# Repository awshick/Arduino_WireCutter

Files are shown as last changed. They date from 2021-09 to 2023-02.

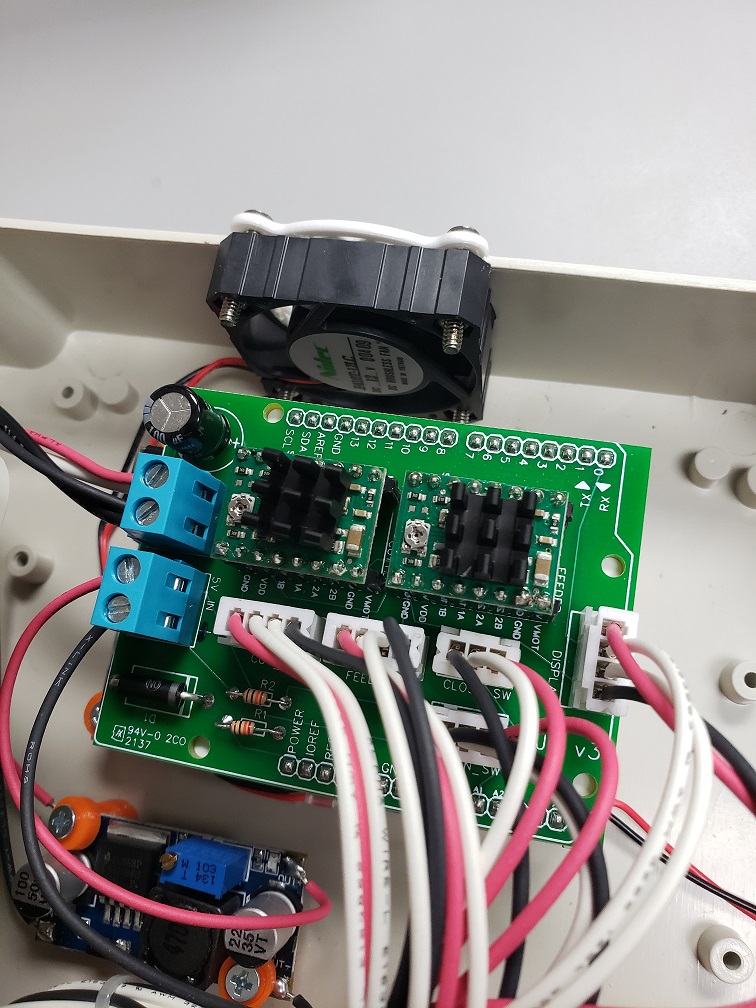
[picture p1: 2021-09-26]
pics/board_view.jpg

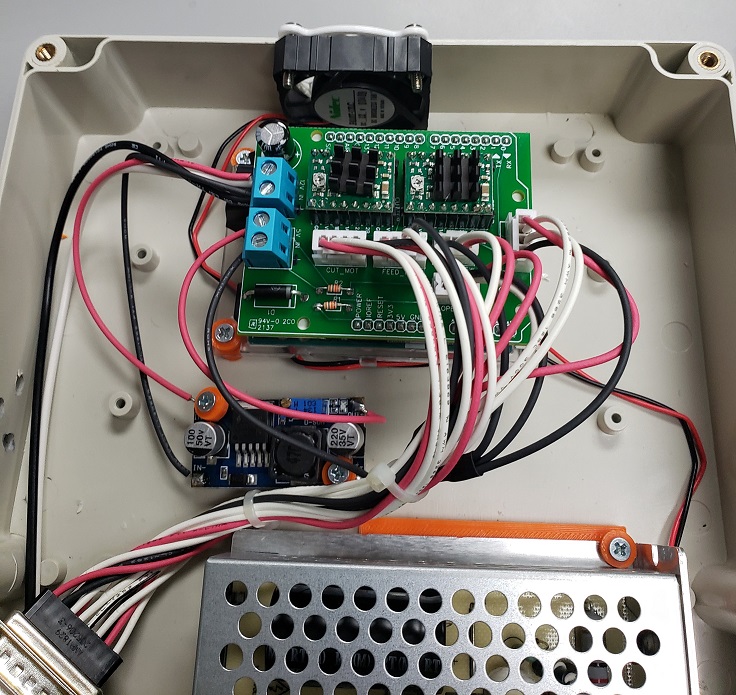
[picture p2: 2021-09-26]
pics/box_view1.jpg

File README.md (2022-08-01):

# Arduino_WireCutter
Arduino wire cutter stripper with nextion display

I'm not a professional. I've worked on my own personal 3d printers for awhile so I'm familiar with arduino and steppers. Never have I done a project like this so its my first from start to finish. I basically saw Mr Innovatives video and wanted a machine similar, but no code or layout was provided. I've made some very simple 3d drawings for the supports and during my trial and error build I decided limit switches where the way I wanted to go. This way I dont care about steps when it comes to cutting the wire (other than feeding wire).
My first nextion HMI - lots of hardships getting through it and the arduino code, again I'm no pro by far. I'm sure there are alot of things that are questionable and/or not correctly done, but I went with what I could figure out.
Please feel free to contribute to the code, if you want to collabrate on this let me know and I'll open the door.
I can be contacted through garzajd3@gmail.com or message on github.

In the pics below is my version of this tool. I went with adding limit switches on the "cutter" stepper so that I do not need to actually know the # of steps for a close/open.
There are a total of 5 3d printed parts: 1 for the feed stepper mount, 1 for the wire tube holder (adjustable to align with cutter), 1 cutter holder, 1 piece the holds both limits switches (mounted to the cutter stepper). 
I've also opted to use a 5:1 stepper for the cutting unit. I was finding that with a standard 1:1 nema 17 sometimes steps would be skipped when trying to cut wire. I'm sure this can be worked out by adjusting linkage, position, etc but I wanted something that would work consistently with alittle more power. 



Sorry this pic is blurry, but it was the only one I took. This is the simple PCB I laid out as a UNO plug-in (shield) for the stepper drivers and connectors. I probably went overkill on the components, but oh well.


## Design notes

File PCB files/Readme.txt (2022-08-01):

Gerber File_BOM:

This is a custom layout I did for this setup.
Nothing special, and can be done on breadboard or with just wire(s).
I also added a 5vdc input, as in my testing the LM7805's looked to power everything
without issue, but nothing actually worked unless arduino was plugged in. I suspect
low current, even with 2 in parallel, but may be a ground/pwr issue on my layout.

Folders:
Mr Innovative Board:
PCB from Mr Innovatives link on youtube. I believe this is the smb version, and not all components
are required for this wire cutter project. However I have not tested this board.

Gerber_Ext_5v:  <-- This is what I will use, as a shield for UNO board.
For use with external 5v (input) to power Arduino board & Display.

old:
Original board I made, included limit switch(s) plug (A1SW, A0SW).
I've found the LM7805's (U2, U3) work, but not impressed with stability, low voltage. Plan to run a buck converter
to drop 12v from main supply down to 5v for display/Uno - 5VIN plug (input voltage, not output).

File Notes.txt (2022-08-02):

8/1/2022:
Modified arduino code(s) for wire length loops. Previously if entering non whole number it would ignore the decimal point on the final length value.
I have it now including the decimal value in the calculation, but still uses a whole number for the step loops - so accuraccy is not 100% but tolerance is alot better now. 
Example - previously was using a calculation of 6.23 stepper motor steps to equal 1mm of wire. If input was for a 100.5mm length it would be should be converted to 
626.115 (100.5 * 6.23). However as it was an integer you would actually get 626 steps. Error would drift more or less depending upon wire length desired. 

10/24/2021:
I've made a few modifications, mostly cosmetic. I've mounted everything on a plastic box, and housed the electronics within it.
I've recieve no contact, so not sure anyone is even following this. If you are reading this and want to make one - reach out to 
me and I'll give you all the help I can.
If you've emailed me and no response, may have gone to spam. Try me at garzajd3@gmail.com (I check this frequently).

This is for 2 stepper setup only. No servo used, as wire is feed into strip point of strippers, and if to be cut stripper is simply fully closed.
Input voltage is 12vDC, not sure of max current draw but I have an 8.5A power supply (way overkill just using what I had on hand).
I did alot of my inital testing with a 12vdc 2amp power brick and it seemed to work just fine.

I used servos in 1/2 step mode, so MS1,MS2,MS3 are needed.
If you want to use in full step, then MS1-MS3 are not required and arduino code will need to be modified
to remove mode selection.

Videos I used to help me with this:
Nextion Display (Huge thanks to Cheap Controls channel. Tons of Nextion stuff here!!!):
https://www.youtube.com/watch?v=VovDHGs1zDk&t=458s

Stepper wiring / usage (Thanks to Gadget Reboot channel):
https://www.youtube.com/watch?v=V7amtlMKsXU

Where this version of the ideal came of,atleast for me (Mr Innovative channel):
https://www.youtube.com/watch?v=Jl6ZATZypAQ&t=1s

Dumb things that took me way to long to figure out:

Using Nextion Editor for HMI programming/layout (https://nextion.tech/nextion-editor/)
I made my own keyboard input, because I could not figure out how to use the built-in one until I was already done.
By then I was not going to go back and update everything.

If using a different Nextion display change this by opening the WireCutter_v5.HMI file in nextion editor
On the top ICON line (after Redo) select the 'Deivce' button to change model/orientation.
Original was built using 5" nextion model NX8048T050. If using a smaller screen (2.4") you will likely need to 
scale images down on the screens (using nextion editor).

The Arduino code may not be as efficient or clean as it should, but I'm not a professional so it just needs to work
reliably. Feel free to improve on.

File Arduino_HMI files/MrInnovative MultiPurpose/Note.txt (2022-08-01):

This setup is based on using the 
Multipurpose v2.0 pcb used in Mr Innovative design.
https://oshwlab.com/sharmaz747/multipurpose-pcb

The Nextion (HMI) is setup for a 2.4" display.

The arduino code does not implement limit switch(s) and nothing
added for servo motor use (if you choose to include in your build).

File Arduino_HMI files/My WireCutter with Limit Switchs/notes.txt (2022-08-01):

8/1/22:
Modified arduino code to adjust length value. Was set to an integer, so if you entered 10.5 it was taking the whole number only (10).
Changed all associated values to float. As the entry is broken into steps (not distance) it will still be a whole number (rounded) for
the loop portion. This should be a closer match to the input length, but still will not be exact.

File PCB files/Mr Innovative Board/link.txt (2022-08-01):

https://oshwlab.com/sharmaz747/multipurpose-pcb_copy_copy_copy

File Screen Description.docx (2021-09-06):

Start Screen:

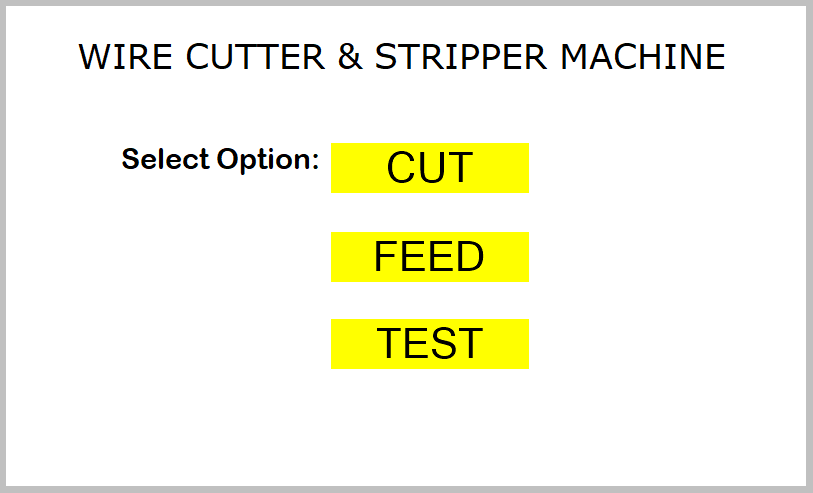
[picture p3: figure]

Select sub screen.

CUT = go directly to cutting wire

FEED = feed wire in/out

TEST = test stepper(s) , check steps and modes.

CUT | Screen 1:

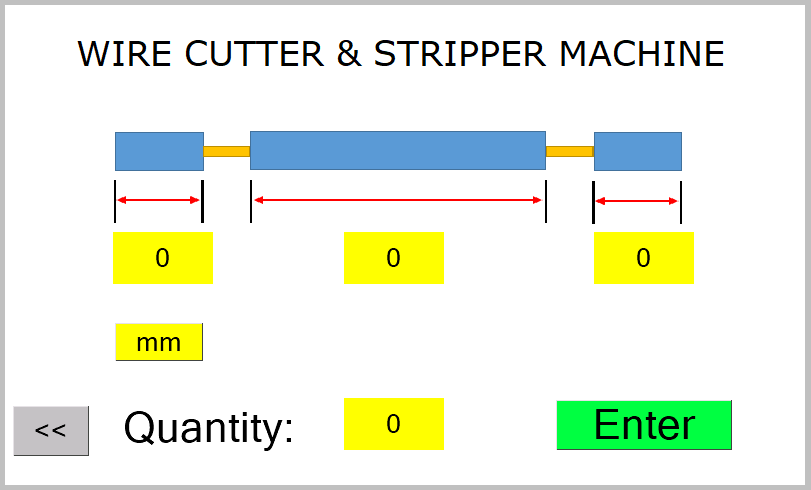
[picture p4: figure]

Enter details here. Can change from mm to inch. Looks like this is +/- .2inch or +/- 2mm

CUT | Screen 2:

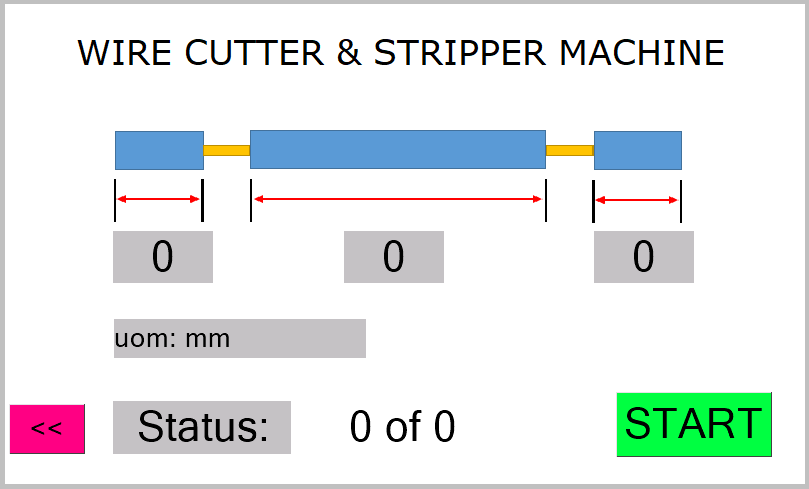
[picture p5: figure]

This is the details that are entered, non-editable on this screen. START begins the process.

Once started a STOP button will be shown, if pressed cycle will stop after current cut.

FEED | Screen 1:

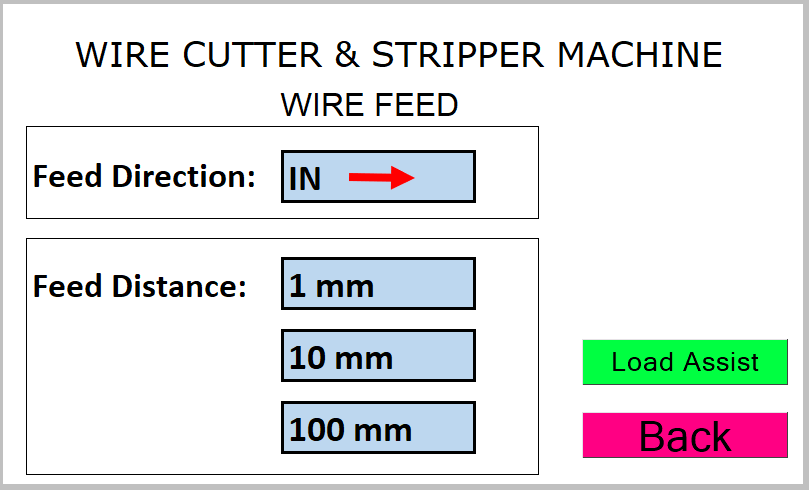
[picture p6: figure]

Select direction to feed wire IN/OUT. Distance button executes action on press. So if you press 10mm it will cycle direction for 10mm. Load Assist button takes to Screen 2.

FEED | Screen 2:

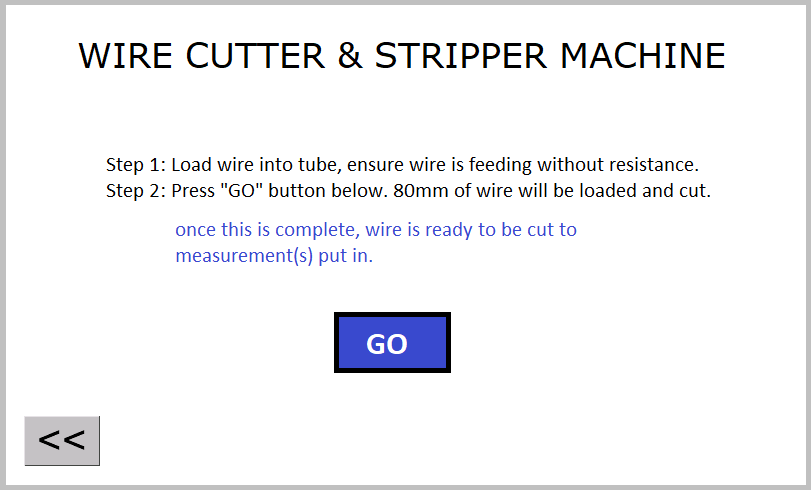
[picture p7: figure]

This is my simple version of loading. Once wire is loaded into tube, this will feed in 80mm and cut. This gives a 0 point to start cutting operation.

TEST | Screen 1:

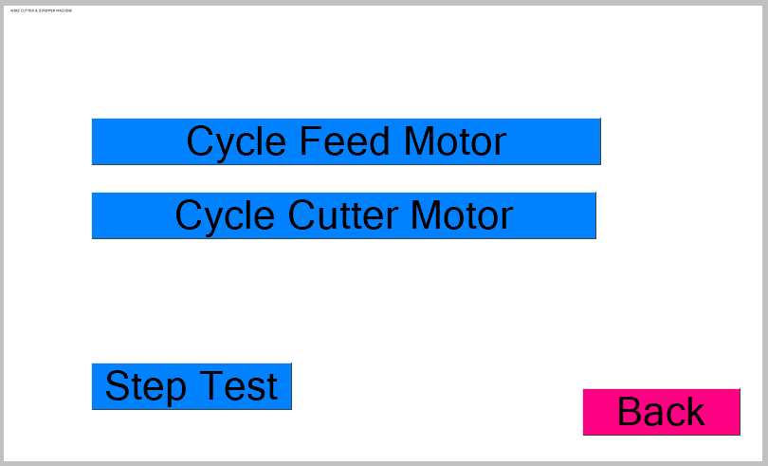
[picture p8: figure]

Simple test will cycle motor chosen.

Step Test leads to Screen 2

TEST | Screen 2:

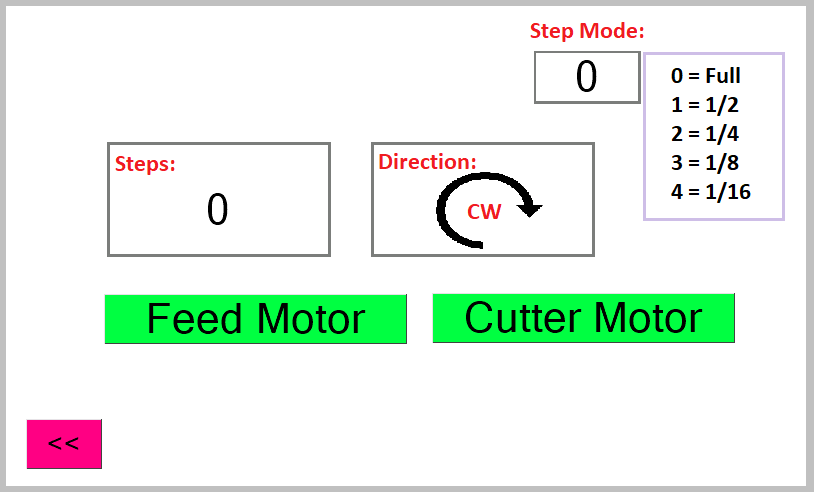
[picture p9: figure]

Not useful for operation, but I added this so I could enter the steps to travel and spin. Helped me determine what mode motor(s) worked best in, as well as how many steps are needed to reach a certain point (stripping, feeding x mm = x steps , etc).

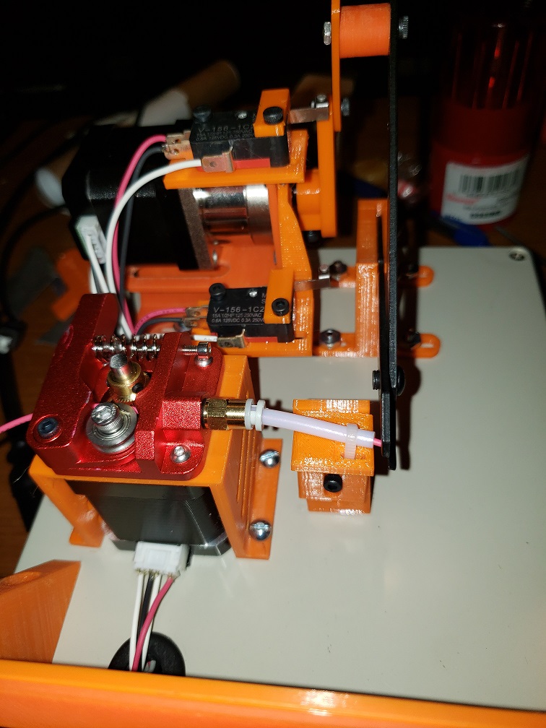
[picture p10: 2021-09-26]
pics/front_view.jpg

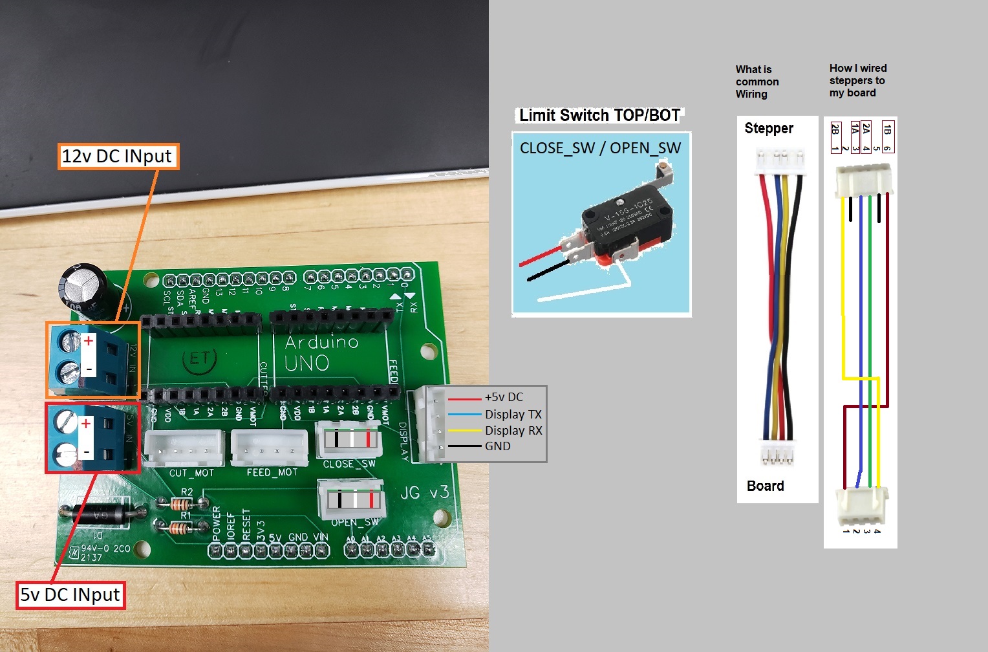
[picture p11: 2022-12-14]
pics/board_wire.jpg

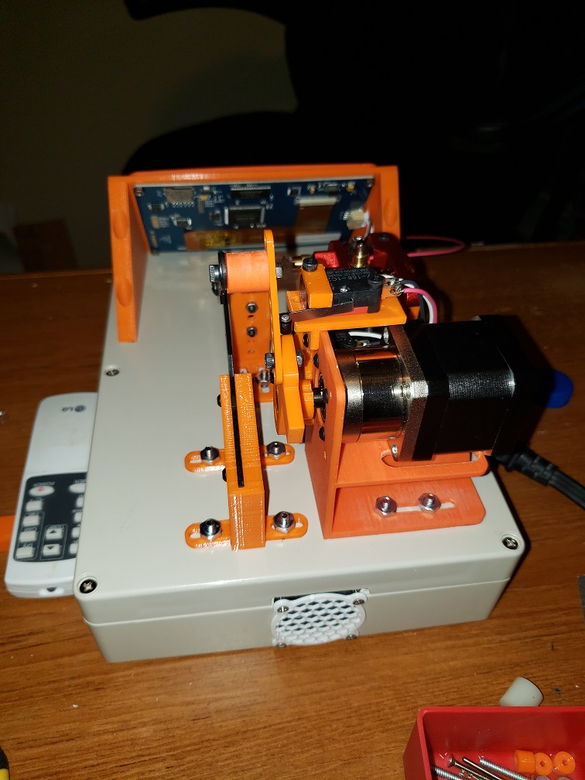
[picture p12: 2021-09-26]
pics/back_view.jpg

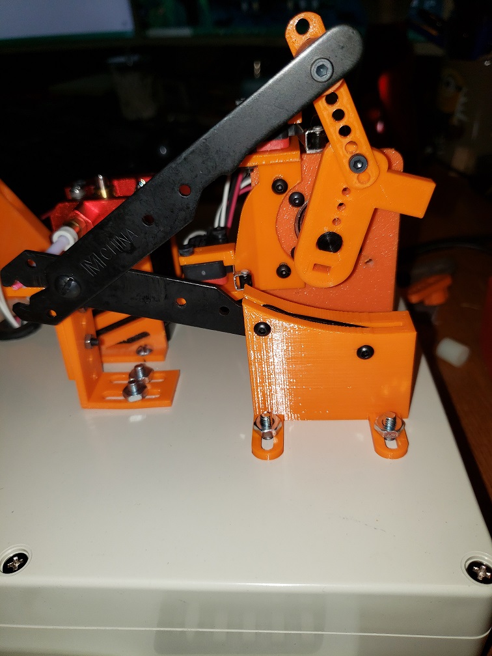
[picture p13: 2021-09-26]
pics/right_view.jpg

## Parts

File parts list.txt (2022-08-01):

These are the parts I used. Many options and models/mfg that do the same thing(s) and may be found cheaper.

Power Supply:	Source=Digikey	Price=$15.09
Description: LM100-23B12	12vdc 100W
https://www.digikey.com/en/products/detail/mornsun-america-llc/LM100-23B12/13168168

Nema 17 5.18:1 Gearbox:	Source=Amazon	Price=$28.59
Description: Usongshine Nema 17 Geared Stepper Motor Gear Ratio 5.18:1 Planetary Gearbox for 3 D Printer DIY CNC Robotics
https://www.amazon.com/gp/product/B07V359RFB/ref=ppx_yo_dt_b_asin_title_o03_s00?ie=UTF8&psc=1

Nema 17:	Source=Amazon	Price$9.99
Description: Twotrees Nema17 Stepper Motor, 4 Lead Stepper Motor Nema 17 Motor with 1m Cable 42BYGH 38MM 1.5A (17HS4401S) for CNC XYZ 3D Printer
https://www.amazon.com/Twotrees-Nema17-Stepper-17HS4401S-Printer/dp/B07Y2SVNGP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

Wire Feed Extruder:	Source=Amazon	Price=$6.99
Description: Gwisdom ENDER3 Extruder Upgraded Replacement, Aluminum MK8 Drive Feed
https://www.amazon.com/gp/product/B07FKD4FZD/ref=ppx_yo_dt_b_asin_title_o03_s00?ie=UTF8&psc=1

Limit Switch:	Source=Amazon	Price=$6.69 (10 pack)
Description: HiLetgo 10pcs V-156-1C25 Lead Limit Switch SPDT Switch Silver Base Contact Roller Swing
https://www.amazon.com/dp/B01MQPQGFQ?psc=1&ref=ppx_yo2_dt_b_product_details

Power Plug/Switch:	Source=Amazon	Price=$8.99
Description: 3Dman 15A 250V Rocker Switch Power Socket Inlet Module Plug 5A Fuse Switch with 18 AWG Wiring 3 Pin IEC320 C14
https://www.amazon.com/gp/product/B07RRY5MYZ/ref=ppx_yo_dt_b_asin_title_o03_s01?ie=UTF8&th=1

Buck Converter:	Source=Amazon	Price=$15.99 (10 pack)
Description: Zixtec 10 Pack LM2596 DC-DC Buck Converter Step Down Module Power Supply DIP Output 1.25V-30V 3A (ZT001)
https://www.amazon.com/gp/product/B07VVXF7YX/ref=ppx_yo_dt_b_asin_title_o04_s02?ie=UTF8&psc=1

Stepper Driver A4988:	Source=Amazon	Price=$9.28 (5 pack)
Description: HiLetgo 5pcs A4988 Stepstick Stepper Motor Driver Module with Heat Sink for 3D Printer Reprap Suitable for Mendel Huxley Arduino
https://www.amazon.com/gp/product/B07BND65C8/ref=ppx_yo_dt_b_asin_title_o04_s03?ie=UTF8&psc=1

Screen (Nextion):	Source=Amazon	Price=$81.97
Description: Nextion Display 5 inch NX8048T050 Resistive Touch Screen HMI TFT LCD Module 800x480 for Arduino Raspberry Pi
https://www.amazon.com/gp/product/B07B4DV86Z/ref=ppx_yo_dt_b_asin_title_o06_s00?ie=UTF8&psc=1

**Optional 2.4" instead:	Source=Amazon	Price=$30.98
Description: NEXTION 2.4 inch Display NX3224T024 Resistive Touch Screen UART HMI LCD Module 320x240 for Arduino Raspberry Pi ESP8266
https://www.amazon.com/WIshioT-Nextion-Display-NX3224T024-Raspberry/dp/B079172C9G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

Wire Cutter: Source=Mcmaster-carr	Price$8.26
Description: 26-12AWG Wire stripper , 5" Steel
https://www.mcmaster.com/wire-strippers/compact-electrical-wire-strippers/

Various M3 screws & nuts. 

ENCLOSURE / BOX PARTS:
Enclosure:	Source=Amazon	Price=$17.98
Description: LeMotech Waterproof Dustproof IP65 ABS Plastic Junction Box Universal Electric Project Enclosure Pale Gray 10.4 x 7.2 x 2.4 inch (263 x 182 x 60 mm)
https://www.amazon.com/gp/product/B0781D5YJH/ref=ppx_yo_dt_b_asin_title_o03_s01?ie=UTF8&th=1

Fan:	Source=Digikey	Price=$4.80
Description: HA40201V4-1000U-A99	40x40x20 12vdc fan
https://www.digikey.com/en/products/detail/sunon-fans/HA40201V4-1000U-A99/6198729

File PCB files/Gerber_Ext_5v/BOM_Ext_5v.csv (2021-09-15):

ID | Name | Designator | Footprint | Quantity | Manufacturer Part | Manufacturer | Supplier | Supplier Part | Price | Pins
1 | TB004-508-02BE | 5V_IN,12V_IN | CUI_TB004-508-02BE | 2 |  |  |  |  |  | 2
2 | 1000uF | C1 | CAP-TH_BD10.0-P5.00-D1.0-FD | 1 | 01EC4294SHC1000UF25V | KNSCHA | LCSC | C503217 | 0.06 | 2
3 | B3B-XH-A(LF)(SN) | CLOSE_SW,OPEN_SW | CONN-TH_3P-P2.50_B3B-XH-A-LF-SN | 2 | B3B-XH-A(LF)(SN) | JST Sales America | LCSC | C144394 | 0.041 | 3
4 | A4988 | CUTTER,FEEDER | A4988 STEPPER MOTOR DRIVER | 2 |  |  |  |  |  | 16
5 | B4B-XH-A-G | CUT_MOT,DISPLAY,FEED_MOT | CONN-TH_B4B-XH-A-G | 3 | B4B-XH-A-G | JST | LCSC | C594232 | 0.196 | 4
6 | 1N5349BG | D1 | DO-201_BD5.3-L9.5-P13.50-D1.4-RD | 1 | 1N5349BG | ON Semicon | LCSC | C232446 | 0.199 | 2
7 | UNO_R3 | P1 | UNO_R3 | 1 |  |  |  |  |  | 32
8 | 10K | R1,R2 | RES-TH_BD1.7-L3.5-P7.50-D0.5 | 2 | RN 1/8W 10K F T/B A1 | TyoHM | LCSC | C433502 | 0.008 | 2

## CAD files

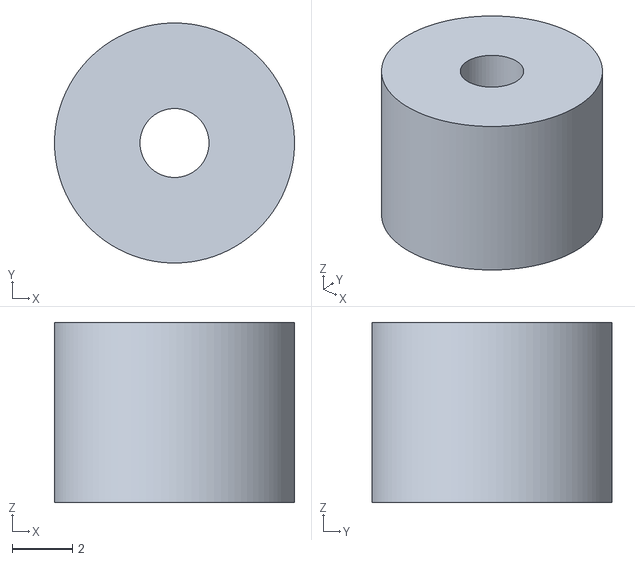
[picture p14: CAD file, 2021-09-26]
3d_printer_files/misc_plasticbox/full_shaft v1.stl
8.00 x 8.00 x 6.00

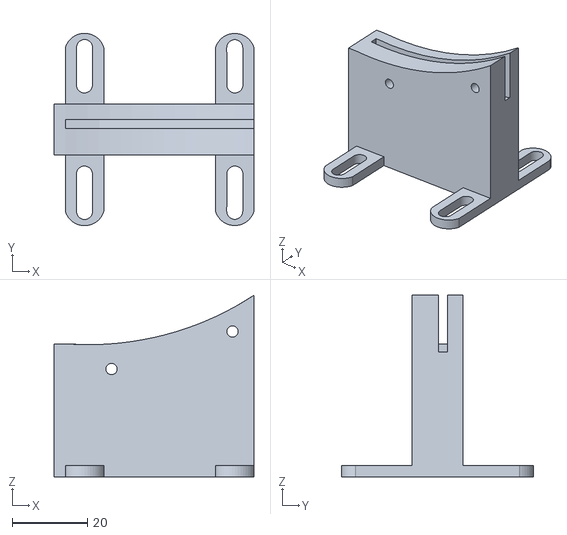
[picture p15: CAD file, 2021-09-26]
3d_printer_files/cutter_holder_adj.stl
53.0 x 51.0 x 48.1

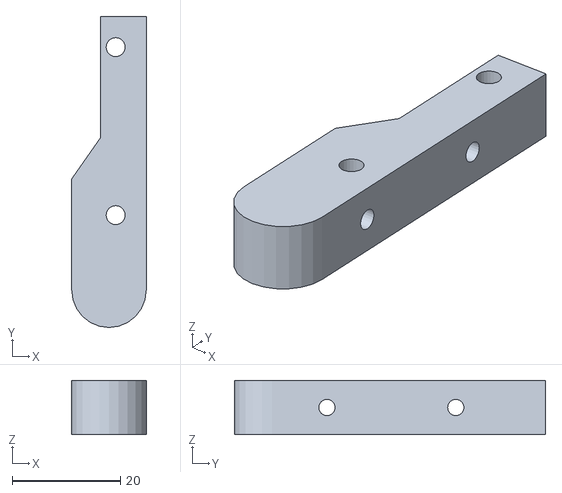
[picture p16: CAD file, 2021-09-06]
3d_printer_files/extruder/fixed_guide.stl
13.8 x 57.4 x 10.00

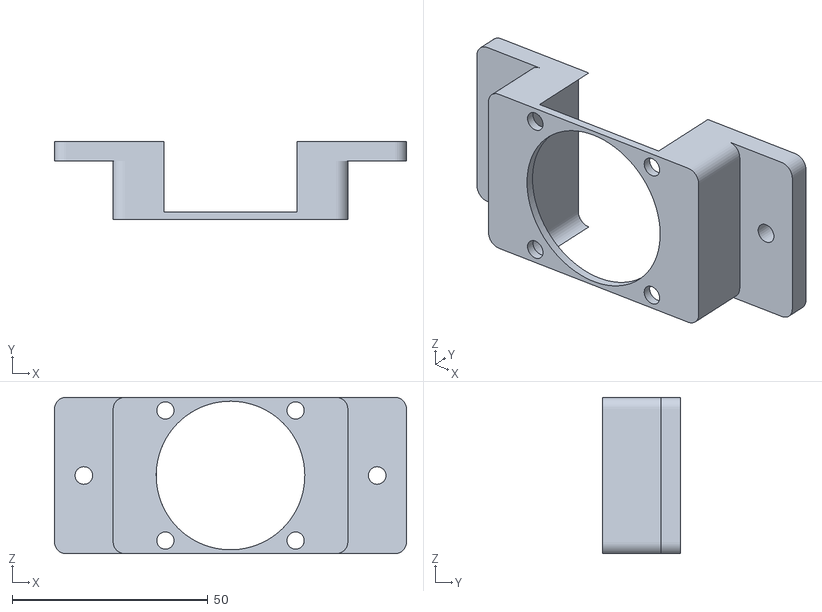
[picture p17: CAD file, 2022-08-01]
3d_printer_files/misc_plasticbox/fan_mount_acutal v2.stl
90.0 x 20.0 x 40.0

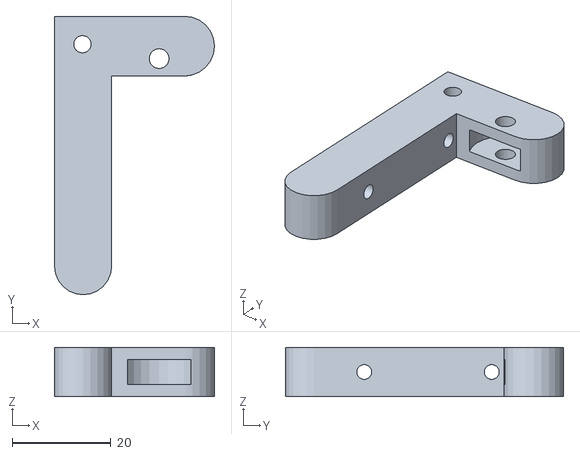
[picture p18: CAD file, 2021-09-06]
3d_printer_files/extruder/swing_handle.stl
32.3 x 56.3 x 10.0

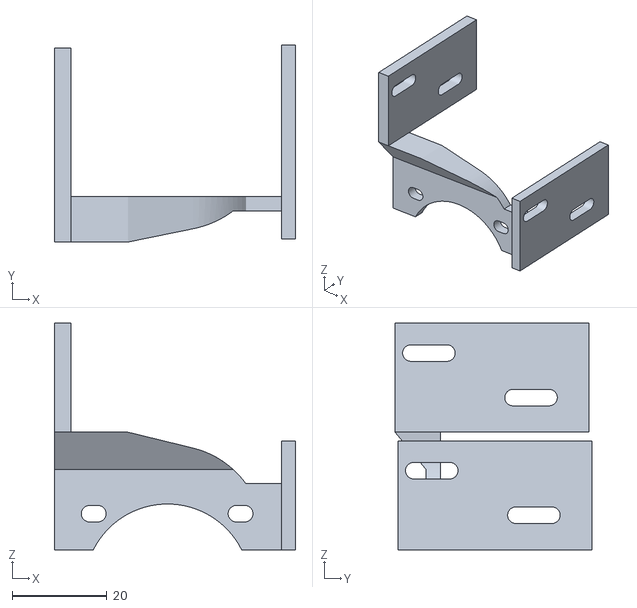
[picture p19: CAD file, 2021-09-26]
3d_printer_files/StopSwitchDual.stl
50.9 x 41.6 x 47.8

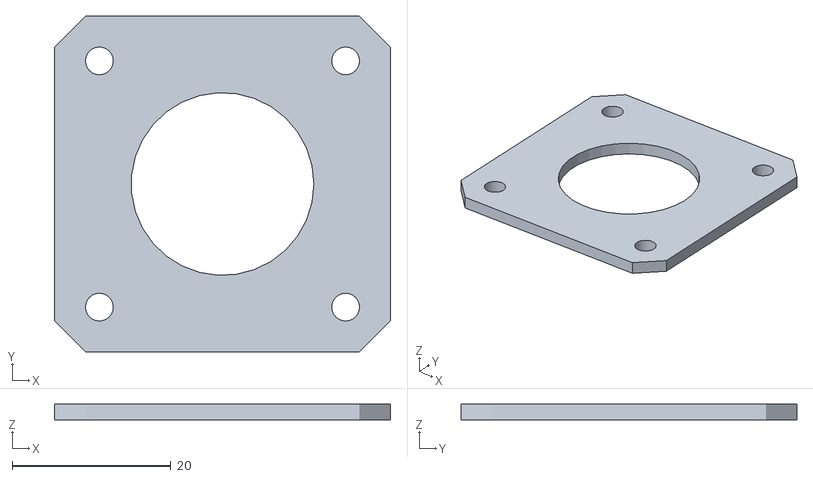
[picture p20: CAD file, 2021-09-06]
3d_printer_files/extruder/spacer.stl
42.3 x 42.3 x 2.00

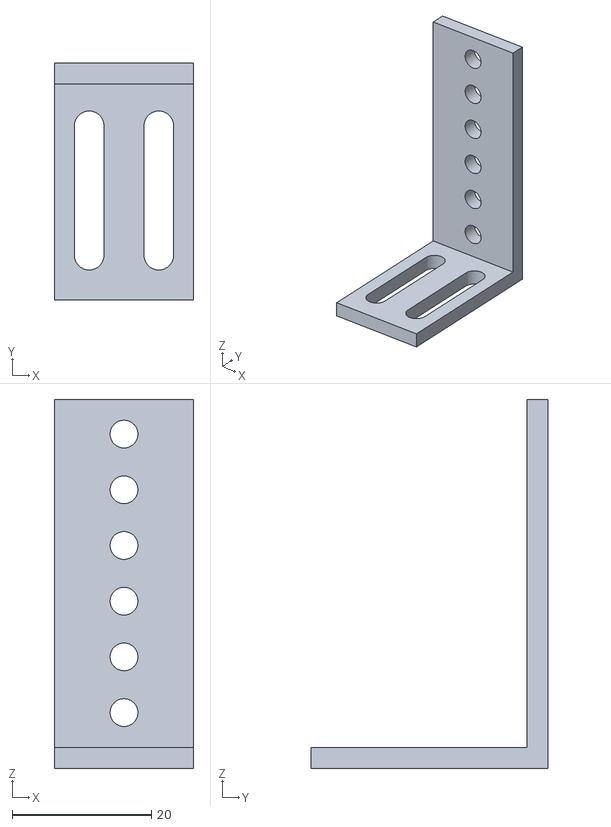
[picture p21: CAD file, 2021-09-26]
3d_printer_files/wire_guide_BOT.stl
20.0 x 34.0 x 53.0

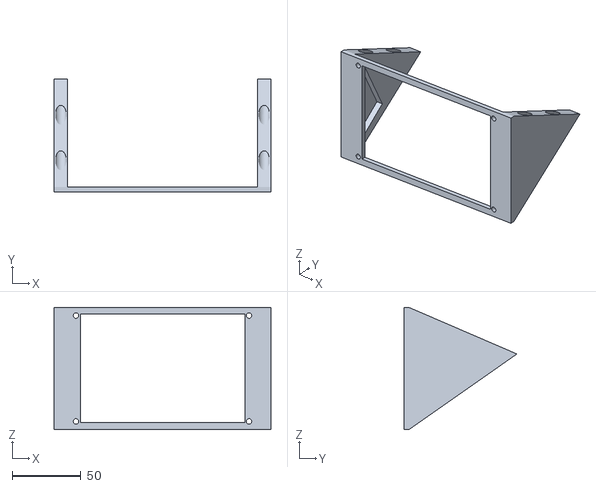
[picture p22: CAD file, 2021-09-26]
3d_printer_files/Display_Stand.stl
158.0 x 82.1 x 89.0

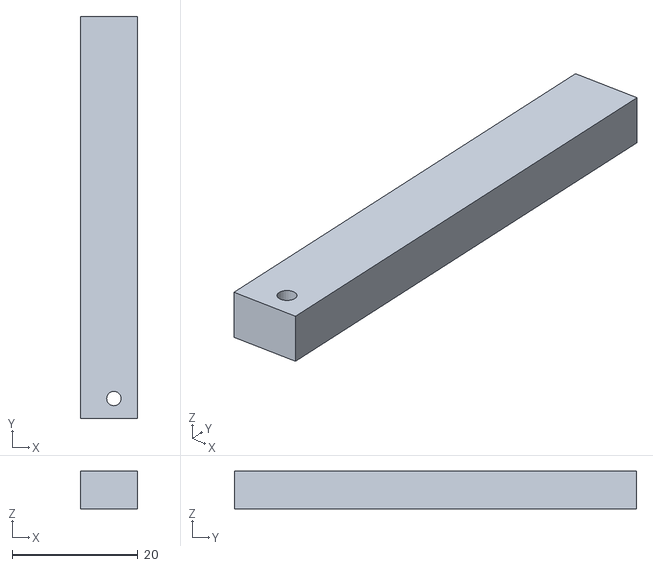
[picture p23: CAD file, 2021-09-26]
3d_printer_files/misc_plasticbox/PS v1.stl
9.00 x 64.0 x 6.00

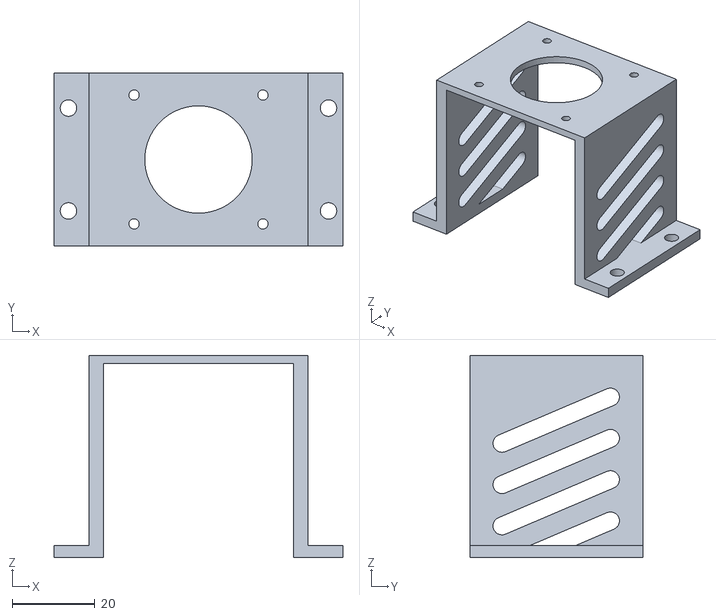
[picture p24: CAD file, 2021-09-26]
3d_printer_files/Feed_Stand.stl
70.0 x 42.0 x 49.0

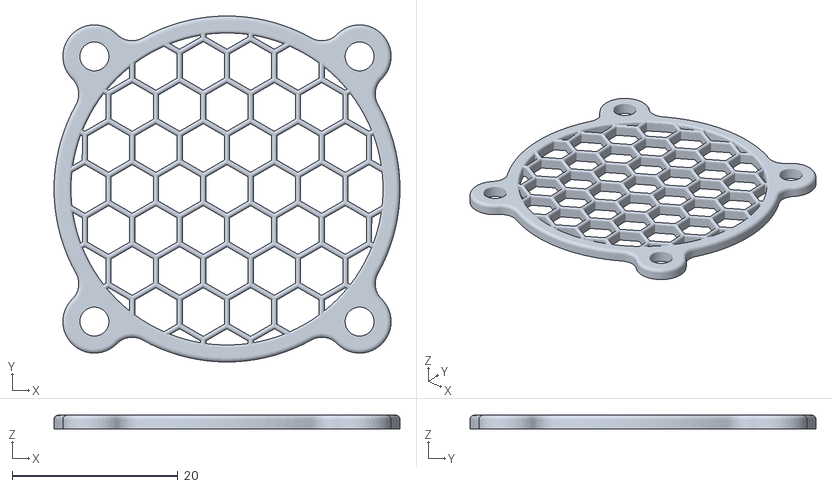
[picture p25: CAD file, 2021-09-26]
3d_printer_files/misc_plasticbox/40mm_Hexaguard.stl
41.8 x 41.8 x 1.65

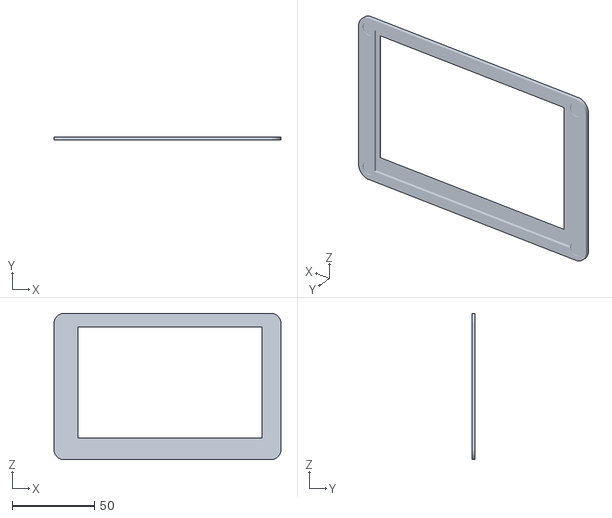
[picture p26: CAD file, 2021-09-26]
3d_printer_files/Display_Bezel.stl
138.0 x 2.00 x 89.0

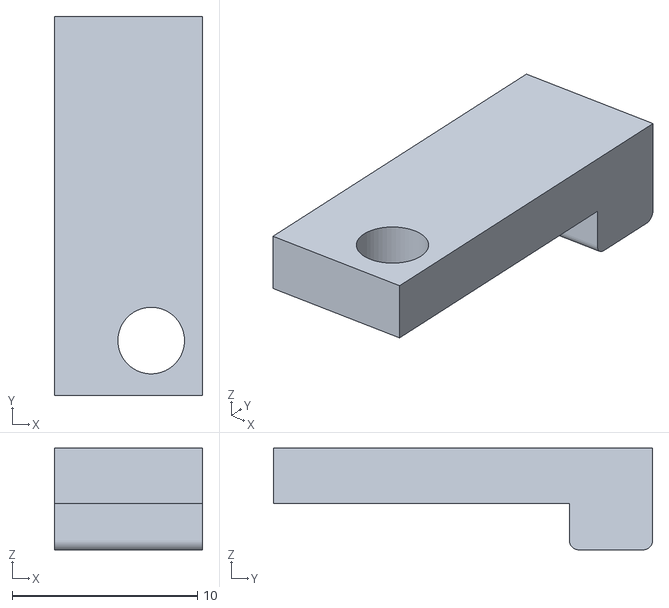
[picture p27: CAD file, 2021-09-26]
3d_printer_files/limitSW_guide.stl
8.00 x 20.5 x 5.50

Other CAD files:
3d_printer_files/Link_Spacer.stl
3d_printer_files/Nema17_5to1_mount.stl
3d_printer_files/partA_5-1_geared.stl
3d_printer_files/wire_guide_TOP.stl
3d_printer_files/Cut_Link.stl
3d_printer_files/fusion/Cut_Link v2.f3d
3d_printer_files/fusion/Display_Bezel v3.f3d
3d_printer_files/fusion/Display_Stand v2.f3d
3d_printer_files/fusion/Link_Spacer v1.f3d
3d_printer_files/fusion/Nema17_5to1_mount v3.f3d
3d_printer_files/fusion/StopSwitchDual v5.f3d
3d_printer_files/fusion/cutter_holder_adj v1.f3d
3d_printer_files/fusion/limitSW_guide v1.f3d
3d_printer_files/fusion/partA_5-1_geared v8.f3d
3d_printer_files/fusion/stepper_stand v8.f3d
3d_printer_files/fusion/wire_guide_BOT v5.f3d
3d_printer_files/fusion/wire_guide_TOP v3.f3d
3d_printer_files/misc_plasticbox/washer v1.stl

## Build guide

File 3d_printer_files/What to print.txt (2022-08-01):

Printed parts:
-Nema17_5to1_mount.stl		Stepper holder for cutting. Drawn to support/mount 5:1 geared stepper
-partA_5-1_geared.stl		Shaft attachment for cutting stepper
-StopSwitchDual.stl		Limit switch(s) mount that attaches to Nema17_5to1_mount.
-limitSW_guide.stl		Cover for limit switch to prevent vertical bending.
-Cut_Link.stl			Link piece attaches to partA.
-Link_Spacer.stl		Spacer from Cut_Link to actual cutter.
-cutter_holder_adj.stl		Mount for actual cutter.
-wire_guide_BOT.stl		Guide/mount for wire tube to cutter 
-wire_guide_TOP.stl		Guide/mount for wire tube to cutter 
-Feed_Stand.stl			Stepper holder for wire feed stepper.
-Display_Stand.stl		Crude holder for Nextion 5" screen.
-Display_Bezel.stl		Bezel for Display_Stand

Parts in folder 'misc_plasticbox' are basic spacers needed for my build. These are basically simple standoffs/fan mount:
Not needed unless using exact same box for mounting:
https://www.amazon.com/gp/product/B0781D5YJH/ref=ppx_yo_dt_b_asin_title_o00_s01?ie=UTF8&psc=1

files under extruder folder are for the feed motor wire feed. A small bearing will be needed.
I've used something like this instead: 
https://www.amazon.com/gp/product/B07FKD4FZD/ref=ppx_yo_dt_b_asin_title_o00_s00?ie=UTF8&psc=1

If above link is broken, google "ender 3 extruder". Cheaper plastic versions or aluminum should work just fine.
The gear will leave tiny teeth impressions in wire, but I've had no issues with wire. Have not found a suitable rubber variant yet.

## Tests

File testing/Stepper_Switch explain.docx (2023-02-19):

The attached code is for the setup I use, which I only use for cutting wire so no stripping is done. I just prefer to do that part manually.

I have 2 limit switches installed. 1 to be hit when the cutter is fully opened and the other when the cutter is fully closed. The types of switches I’m using are these:

https://www.amazon.com/gp/product/B01MQPQGFQ/ref=ppx_yo_dt_b_search_asin_title?ie=UTF8&psc=1

My limit switches have 5v , Ground through a 10k resistor, and a sense wire hooked to them. The 10k resistor is necessary because the 5v will be shorted to ground to provide a low signal on A0 pin when switch is triggered. If the resistor is not included this would cause a direct short to ground on the Arduino / power supply with no load (that would be bad). A different resistor value may work, but I just used a 10k ohm and it worked fine.

Example:

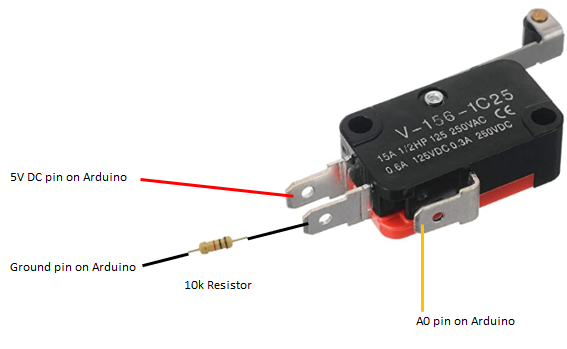
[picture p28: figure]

In my Arduino code I assign a variable for each limit switch pin. On the Arduino uno A0 is identified as pin 14, and A1 is identified as pin 15.

In the beginning of the code these lines are for both switch setup:

int intPinA = 0; //will be used for cutter stop switch for cutting

int intPinB = 0; //will be used for cutter stop switch for opening

int openLimit = 14; //default open limit is set to 14 for A0 - will change if A1 is hit instead using defineLimit()

int closeLimit = 15; //default close limit is set to 15 for A1 - will change if A0 is hit instead using defineLimit()

pinMode(14, INPUT); //using Analog 0 as digital I/O for cutter open stop switch

pinMode(15, INPUT); //using Analog 1 as digital I/O for cutter close stop switch

Explanation:

Int intPinA=0; -This line just creates an integer variable named intPinA with a value of 0. The same is true for the intPinB line. This will be used later to determine the switch state. 0 = switch open , 1 = switch closed.

Int openLimit=14; -This line creates an integer variable named openLimit with a value of 14. This is used to identify my openLimit switch hooked to pin 14 on the Arduino.

Further down in the code, the switches are read / used in the functions ‘closeCutter()’ ‘openCutter()’ ‘stripCutter()’.

Example:

digitalWrite(enablePinB,LOW); //enable driveB

digitalWrite(dirPinB,LOW); //will be turning CCW

for(int x = 0; x < 5000; x++) { //putting in stupid high number for steps, as we will utilize switch for stop

intPinB = digitalRead(openLimit); //get A0 state LOW/HIGH

if(intPinB == 1) { //switch has not been hit so run

digitalWrite(stepPinB,HIGH);

delayMicroseconds(500);

digitalWrite(stepPinB,LOW);

delayMicroseconds(500);

}else { //switch has been hit, move back to reset switch

digitalWrite(dirPinB,HIGH); //reverse to CW direction to move off of switch

delay(500);

while(intPinB != 1) { //move until switch goes back to open

intPinB = digitalRead(openLimit); //re-read A0 state for change

digitalWrite(stepPinB,HIGH);

delayMicroseconds(800);

digitalWrite(stepPinB,LOW);

delayMicroseconds(800);

}

break; //exit loop to stop motor from cont to try and move

}

}

digitalWrite(enablePinB,HIGH); //disable driveB

delay(800);

}

Breakdown of each line:

digitalWrite(enablePinB,LOW); -- this simply sets my enable pin to low on the stepper driver. This basically turns the stepper driver ON and should make it so the stepper can be controlled.

digitalWrite(dirPinB,LOW); – Sets the enable pin to low on the stepper driver. Low = turn counter clockwise, High = turn clockwise.

for(int x = 0; x < 5000; x++) { -- This is a loop that will run 5000 times. Used to pulse the stepper 5000 times for movement. Stepper should not actually step 5000 times because it will hit a limit switch and stop (seen here a few lines below)

intPinB = digitalRead(openLimit); --This is where I am actually reading the switch state. As the ‘openLimit’ variable was set to ‘14’ in the beginning of the code, we are setting the intPinB variable to be what state pin 14 is in (1 or 0). If the switch has not been triggered this state should be 1, if the switch has been triggered this state should be 0.

if(intPinB == 1) { --if we read a 1 in the above line, we will continue to step the motor 1 step.

digitalWrite(stepPinB,HIGH);

delayMicroseconds(500);

digitalWrite(stepPinB,LOW);

delayMicroseconds(500);

}else { --if we read a 0 in the above line, we will back the stepper up until the switch reads a 1 indicating the switch is not triggered.

--The below lines are in a loop until the motor turns clockwise and the switch is no longer triggered.

digitalWrite(dirPinB,HIGH); //reverse to CW direction to move off of switch

delay(500);

while(intPinB != 1) { //move until switch goes back to open

intPinB = digitalRead(openLimit); //re-read A0 state for change

digitalWrite(stepPinB,HIGH);

delayMicroseconds(800);

digitalWrite(stepPinB,LOW);

delayMicroseconds(800);

}

break; --now we simply break the operation, stopping the initial for loop where the stepper would run up to 5000 steps.

}

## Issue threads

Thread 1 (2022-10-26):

call you

daivu2020, 2022-10-26:

daivu2020, 2022-10-26:
i want to call you
daivu4651@gmail.com

awshick, 2022-10-26:
Hello.
I'm not sure where you would be calling from, but I'm typically not
available until after 4:30pm (Central).
If during the week, you can call me (after 4pm) @ 972-994-8521.
I havent worked with this cutter in awhile so I'm abit rusty, but should be
able to answer the basics.

-Joe

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

daivu2020, 2022-11-01:
I want your house to give me a program like mr innovative I will pay for you
Can you help me if you have free time?

awshick, 2022-11-01:
Everything is open source and on github. So I'm not sure what you are
asking for exactly.
Are you wanting a built unit or some kind of software customization?

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

daivu2020, 2022-11-02:
I would like to ask you to give me an HMI program with only "CUT"
and arduino program

daivu2020, 2022-11-02:
because in your program there are 3 parts "CUT" "TEST".......
and arduino program too
I use arduino nano
a4988
servo 90s
nema 17

awshick, 2022-11-02:
Ok I can understand that. But you would need to be able to edit/modify the
arduino code, as the steps for a full cut (on your stepper) may be
different than mine.
Are you familiar with arduino coding enough to do this?
Are you still wanting to be able to input the length, and quantity, for the
cut or will it be the same every time? Or are you just looking for a simple
"press here" button that executes the same function every time (same length
of wire no matter what)?

Do you have a schematic for how your drivers (a4988) are wired?
I do not use any servo's in my build, and if you are just "cutting" the
wire I dont see the need for a servo - so what is it doing?

I can help you make the code, for what you want, but I need specific
details for all of this. What size/resolution is your nextion screen, what
do you want to actually see when powered on, what do you want to be able to
enter (wire details), etc.
It would be best for me to rough code the arduino and HMI code, and walk
you through the steps involved to modify/customize for your use.

Also, judging by the time your emails are sent, it looks like we are on
quite a huge time difference. May I ask where you are located? Worse case I
may be able to do a teams meeting or something similar to show you the code
and walk you through it.

-Joe

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

daivu2020, 2022-11-02:
I come from Vietnam

daivu2020, 2022-11-02:
do you use facebook or instagram?

daivu2020, 2022-11-02:
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

ivanichy77, 2023-02-17:
hello

I have tried your example and it works perfect, thank you very much for your contribution.
I have another nextion of another size but I have not had a problem importing your code,

I am inexperienced in programming nextion,
It's been a couple of weeks I want to put two limit switches to fix a dc motor and make it turn until it detects a sensor and not by time, with the limit switches to know that it's in the correct position and to turn or stop.

when i do the arduino code to know the position and rotate until it detects the other limit switch, i put the new code in the loop before the readserial and it works until i connect the screen.

Do you know how to make the code do a digitalRead , I always get the same value when the nextion is connected, if I put digital wirte in some void it does them well but it doesn't read them. it only reads when i disconnect the nextion

you can help? thank you so much

awshick, 2023-02-17:
If you can send me your arduino code? Also what pin or pins are your limit
switches on?

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

ivanichy77, 2023-02-18:
As I have told you, I don't know how to interrupt the connection of the nextion micro so that it can perform the digital read, or how to do the reading, I have been seeing examples of the nextion that read the value and show it on the screen, but I can't do it work in your example.
  I'm a little lost

As I have told you, I don’t know how to interrupt the connection of the Nextion so that it can perform the digitalRead or how to do the reading
I have been seeing examples of the Nextion that read the value of a potentiometer and show it on the screen but I can’t do the read and work in your example
I´m a little lost.

The new pins are

const int motorDC = 10;       //motor dc 120 r.p.m
const int sensorA = 8;        //limit swicht that detect that the motor are position initia Al 0º
const int sensorB = 9;        //limit switch that detects that the motor has turned to position B 180º
int valA = 0;
int valB = 0;

In the Void setup() I add,

 pinMode(motorDC, OUTPUT);
 pinMode(sensorA, INPUT_PULLUP);
 pinMode(sensorB, INPUT_PULLUP);

void openCutter()  I change it for

valA = digitalRead(sensorA);     //Read limit swttch position opne 0ª
 if  (valA == 0){
digitalWrite(motorDC,HIGH);
}else {
 digitalWrite(motorDC,LOW);
}
 delay(500);

void closeCutter() {

 valB = digitalRead(sensorB);     //Read limit swttch position close 180º
 if  (valB == 0){
digitalWrite(motorDC,HIGH);
}else {
 digitalWrite(motorDC,LOW);
}
 delay(500);
}

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

awshick, 2023-02-18:
Ok.
So your first email stated that your *not *having a problem importing the
code on a different nextion screen, is that correct?
Also, just so I understand a little better:
 - are you trying to use a standard DC motor or a stepper motor? (If
standard DC, what pin(s) are driving the motor or are you using pin 10?)
 - what type of arduino? (Nano / uno / etc)

I personally use limit switches on my setup to determine when the stepper
has opened the cutter and also when it has closed it. I do this because I
do not care about the stripping function and only want to cut wire at
length.
If that is the function you are trying to achieve, I may be able to explain
how my setup is for you.

As for the nextion screen programming, this is new to me also. They are
interesting to use but the code for arduino and the code for nextion are
different.
The code for reading switch state(s) would need to be in the
routine/function. So if the arduino is running the "CUT" code, you would
have it read the switch after every movement of the stepper. Once the
switch is triggered then we would have a statement that breaks the code and
stops the motor loop routine.
If you are not using a stepper motor, and only a dc motor, then this may
take some trial and error - but would be a similar process I would think.

Let me know what motor type you are using , and I'll go from there. If all
you need is to figure out where to code the switch I can help with that
easy enough as I already have the code.

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

daivu2020, 2023-02-18:
Thank you very much

ivanichy77, 2023-02-18:
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

Yes I´ve a Nextion enhaced 3.5 and I import your code .HMI , I have only rescaled some button

> - are you trying to use a standard DC motor or a stepper motor? (If
> standard DC,
> what pin(s) are driving the motor or are you using pin 10?)
Standar motor 24V with a rele on pin 10
> - what type of arduino? (Nano / uno / etc)
Mega 2056
>
> I personally use limit switches on my setup to determine when the stepper
> has opened the cutter and also when it has closed it.

Yes I want it, for cut a ribbon

> I do this because I do not care about the stripping function and only want to cut wire at
> length.
> If that is the function you are trying to achieve,

Yes, when I close it, I will keep it closed for a while depending on the thickness of the ribbon.

in the future I will put a stepper motor to rotate the blade and cut at an angle,
Like when in your example you put the first cut and mark the cable to strip, I want to set an angle and rotate the blade to cut, but I need check that the blade is in the open position or opening, so that the stepper motor can rotate it.
I also want to put a limit switch that detects when there is no ribbon to cut and pause the cycle
Now I want know how to read a  pin

> I may be able to explain
> how my setup is for you.
Thanks
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

I sustituye your void openCutter() by this:

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

But don’t read the pin

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
awshick, 2023-02-19:
Ok now I see my confusion. I'm receiving emails directly and through github. Also an issue was opened and then continued into this one.  So @ivanichy77 if you did not receive my email with file(s) attached (same text as above comment) you can get the files I attached here:  https://github.com/awshick/Arduino_WireCutter/tree/main/testing
Also I see youtube link was covered up. But the channel name is Cheap Controls. Tons of nextion step by step programming videos from there. Great resource if needed.

awshick, 2023-02-19:
@ivanichy77 Ok the file(s) I emailed to you had some issues.
I tried to duplicate your setup on my bench with a Mega2560 and has some errors.
So I've corrected the files and uploaded them here:
https://github.com/awshick/Arduino_WireCutter/tree/main/testing

So again delete the file(s) you received in my email, if you received it, and use the files uploaded here on github.

ivanichy77, 2023-02-19:
Hello, I have also been confused, I thought I was only writing to you by mail and not in the thread, I have been reading your file with the limit switch, but I did not use it because in the configuration of the stepper motors there are three variables that I did not understand , if in that example you explain very well how to use the SwitchesThe fact that the motor does not stop in the position due to inertia is not going to be a problem, I think it will stop very quickly and I can correct that inertia time, physically advancing the switchHe visto el nuevo codigo in the new folder that you have created, the hmi, ino and the images, I really appreciate your involvement and help that you are offering,I try it and I comment, and I learn your way of using digitalreadThanksEl 19 feb 2023, a las 7:45, awshick ***@***.***> escribió:
@ivanichy77 Ok the file(s) I emailed to you had some issues.
I tried to duplicate your setup on my bench with a Mega2560 and has some errors.
So I've corrected the files and uploaded them here:
https://github.com/awshick/Arduino_WireCutter/tree/main/testing
So again delete the file(s) you received in my email, if you received it, and use the files uploaded here on github.

—Reply to this email directly, view it on GitHub, or unsubscribe.You are receiving this because you were mentioned.Message ID: ***@***.***>

ivanichy77, 2023-02-19:
Hello, I have also been confused, I thought I was only writing to you by mail and not in the thread, I have been reading your file with the limit switch, but I did not use it because in the configuration of the stepper motors there are three variables that I did not understand , if in that example you explain very well how to use the SwitchesThe fact that the motor does not stop in the position due to inertia is not going to be a problem, I think it will stop very quickly and I can correct that inertia time, physically advancing the switchI have seen and read the test folder, all very detailed, you have created the hmi, ino and the images, I really appreciate your involvement and help that you are offeringI try it in my mega and I comment and I learn your way of using digitalreadThanksEl 19 feb 2023, a las 7:45, awshick ***@***.***> escribió:
@ivanichy77 Ok the file(s) I emailed to you had some issues.
I tried to duplicate your setup on my bench with a Mega2560 and has some errors.
So I've corrected the files and uploaded them here:
https://github.com/awshick/Arduino_WireCutter/tree/main/testing
So again delete the file(s) you received in my email, if you received it, and use the files uploaded here on github.

—Reply to this email directly, view it on GitHub, or unsubscribe.You are receiving this because you were mentioned.Message ID: ***@***.***>

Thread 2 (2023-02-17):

dude with digitalRead

ivanichy77, 2023-02-17:
hello

I have tried your example and it works perfect, thank you very much for your contribution.
I have another nextion of another size but I have not had a problem importing your code,

I am inexperienced in programming nextion,
It's been a couple of weeks I want to put two limit switches to fix a dc motor and make it turn until it detects a sensor and not by time, with the limit switches to know that it's in the correct position and to turn or stop.

when i do the arduino code to know the position and rotate until it detects the other limit switch, i put the new code in the loop before the readserial and it works until i connect the screen.

Do you know how to make the code do a digitalRead , I always get the same value when the nextion is connected, if I put digital wirte in some void it does them well but it doesn't read them. it only reads when i disconnect the nextion

you can help? thank you so much

awshick, 2023-02-19:
Responding through email sent. If your not receiving my email(s) please let me know here. Thanks.

ivanichy77, 2023-02-21:
hello, Reading the code and your explanations, I couldn't make the test
code work. After reading and rereading and seeing that your code was
correct and very well explained, I realized that the connection that made
the switch was wrong. Stepper_Switch explain.docx is a great help but I had
to change the connection com ---> A0 pin arduino by com ---> GND NO --> 10k
resistor --> GND by NO --> 10 resistor --> 5v dc NO --> A0 arduino pin
(read pin) Thank you for your explanations, I will continue with the code
and assembly, and I will comment on the results

thank you

El dom, 19 feb 2023 a las 5:19, awshick ***@***.***>)
escribió:

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

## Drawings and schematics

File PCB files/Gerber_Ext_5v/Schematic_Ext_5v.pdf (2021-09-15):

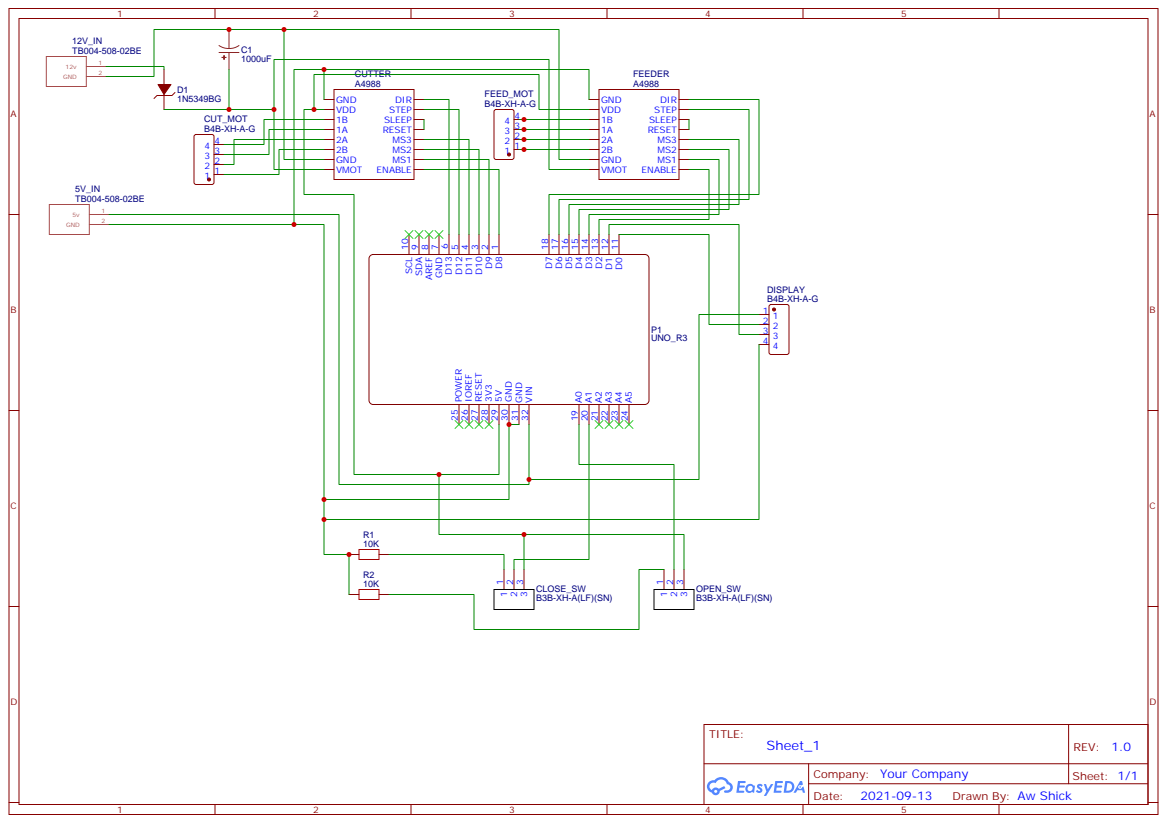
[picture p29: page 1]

Drawn By: Aw Shick

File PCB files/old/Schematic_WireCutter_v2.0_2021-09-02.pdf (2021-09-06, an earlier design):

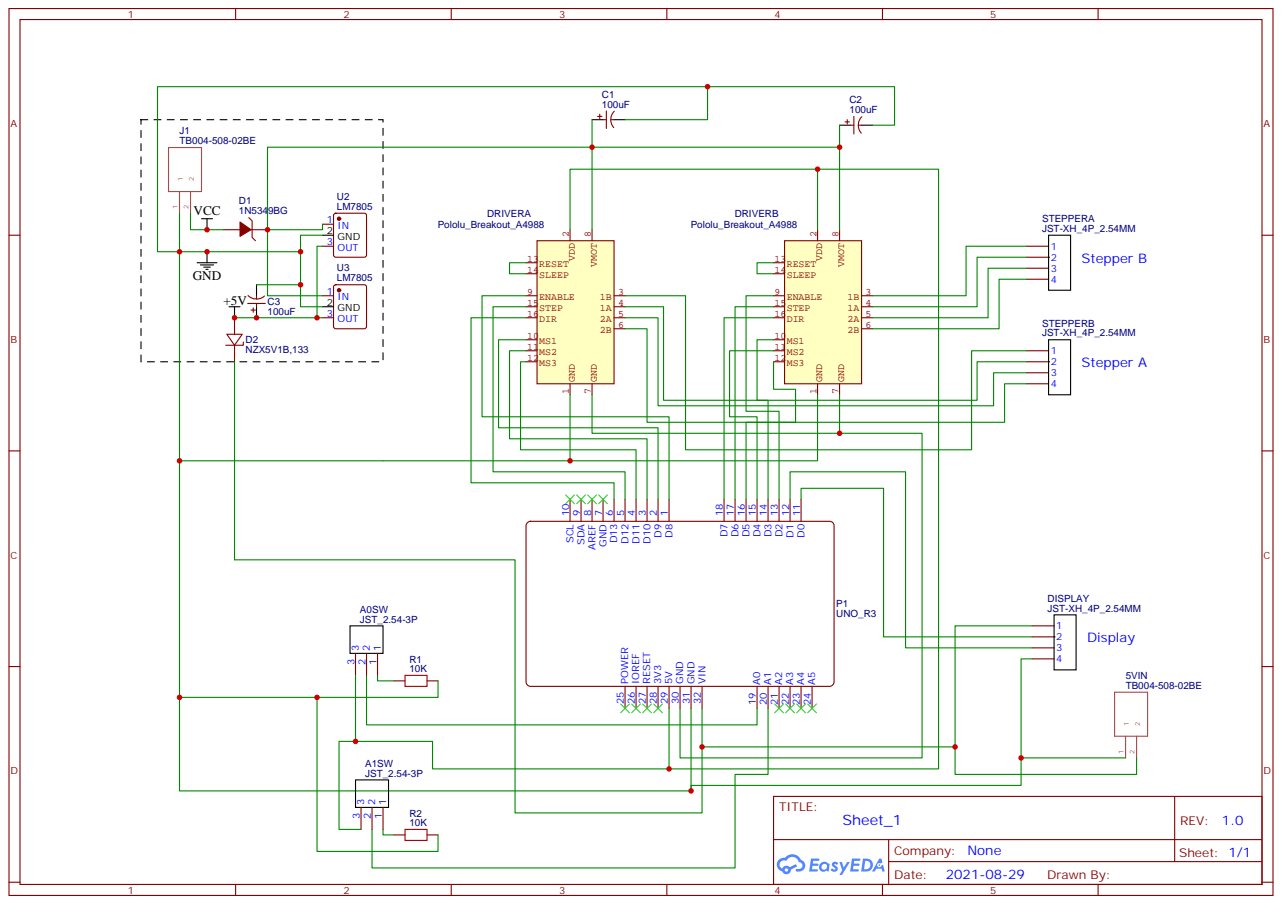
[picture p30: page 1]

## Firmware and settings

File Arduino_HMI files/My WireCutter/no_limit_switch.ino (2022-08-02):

//#include <Nextion.h>    //used for MCU through HMI Editor only -- must remove or comment out when using actual screen
//#define nextion Serial  //used for MCU through HMI Editor only -- must remove or comment out when using actual screen

//-------------User Variables------------------------------------------------------------------------------------------------------------------------------------------------------------
//  These may change depending upon the setup: Stepper steps for rotation, Stepper mode, etc
//  My steppers are 200 full steps for a full rotation (360 degrees), so numbers below based on that.
//  Should be the only variables that would need to be changed in code.
float actualLength = 6.23;      //will be used in cutLoop for steps per mm      **I've calculated 623 steps for 100mm, so 623/100=6.23 which should be 1mm. Change this value as required.
int aCycle = round(actualLength);   //dont change this
int stripSteps = 475;         //total steps needed for Cutter to make STRIP cut --will adjust depending upon wire AWG but I plan to use 22 AWG.
int openSteps = 500;          //total steps needed for Cutter to fully open, half to assume worse case is cutter is fully closed.
int closeSteps = 500;         //total steps needed for Cutter to fully close, half to assume cutter is fully opened.
int feedStepMode = 1;         //step mode for feed motor. 0=Full, 1=1/2, 2=1/4, 3=1/8, 4=1/16
                              //You may want to change this for speed/efficiency depending upon the setup.
int cutStepMode = 1;          //step mode for opening/closing cutter. 0=Full, 1=1/2, 2=1/4, 3=1/8, 4=1/16
                              //You may want to change this for speed/efficiency depending upon the setup. 
           
                
//---------------------------------------------------------------------------------------------------------------------------------------------------------------------------------------


//-------------------Pin Variables-----------------------------------------------------------------
  //pin assigments
const int enablePinA = 2; //Stepper1 Feed Motor
const int ms1A = 3;       //Stepper1 Feed Motor
const int ms2A = 4;       //Stepper1 Feed Motor
const int ms3A = 5;       //Stepper1 Feed Motor
const int stepPinA = 6;   //Stepper1 Feed Motor
const int dirPinA = 7;    //Stepper1 Feed Motor

const int enablePinB = 8; //Stepper2 Cut Motor
const int ms1B = 9;       //Stepper2 Cut Motor
const int ms2B = 10;      //Stepper2 Cut Motor
const int ms3B = 11;      //Stepper2 Cut Motor
const int stepPinB = 12;  //Stepper2 Cut Motor
const int dirPinB = 13;   //Stepper2 Cut Motor

//-------------------Function Variables--------------------------------------------------------------
//CutLoop variables, sent from cut page
float preStripValue = 0;      //will be used to store precut(strip) for cutLoop
float lengthValue = 0;        //will be used to store cut length for cutLoop
float postStripValue = 0;     //will be used to store postcut (strip) for cutLoop
int qtyValue = 0;             //will be used to store qty for cutLoop
String uom = "";              //will be used as unit of measure (I=inch, M=mm)
//int actualLength set @ top of variables as this may vary depending upon stepper/driver.
String myStop = "";           //will be used in cutLoop to monitor for STOP being pressed
int vRun = 1;                 //will be used in cutLoop to interrupt if STOP pressed

//feedLoop variables, sent from feed page  - feed wire in/out    (vDirection, vLength)
String vDirection = "";
unsigned long vLength;    //might be able to change to Int

//testLoop variables, sent from test page  - cycle steppers      (vMotor)
int vMotor;     //might be able to change to String 
 
//stepLoop variables, sent from steptst page - run stepper x pulses , x step mode
//will use vDirection for step direction 
int vMode = 0;                //Step Mode to run motor in 
int vStep = 0;                //Steps to take
String sMotor = "";

String dfd = "";          //Serial data container, data from display
//-----------------------------------------------------------------------------------------------

void setup() {
 Serial.begin(9600);    //used to monitor - arduino recieve

 pinMode(enablePinA, OUTPUT);
 pinMode(ms1A, OUTPUT);
 pinMode(ms2A, OUTPUT);
 pinMode(ms3A, OUTPUT);
 pinMode(stepPinA, OUTPUT);
 pinMode(dirPinA, OUTPUT);
 pinMode(enablePinB, OUTPUT);
 pinMode(ms1B, OUTPUT);
 pinMode(ms2B, OUTPUT);
 pinMode(ms3B, OUTPUT);
 pinMode(stepPinB, OUTPUT);
 pinMode(dirPinB, OUTPUT);

 digitalWrite(enablePinA,HIGH); //disable driveA
 digitalWrite(enablePinB,HIGH); //disable driveB
//Update actualLength based on step mode (if 1/4 step then it wont be the same as if full step)
if(cutStepMode==1){
  actualLength=actualLength * 2;
  stripSteps=stripSteps * 2;
  aCycle = aCycle * 2;
}else if(cutStepMode==2) {
  actualLength=actualLength * 4;
  stripSteps=stripSteps * 4;
  aCycle = aCycle * 4;
}else if(cutStepMode==3) {
  actualLength=actualLength * 8;
  stripSteps=stripSteps * 8;
  aCycle = aCycle * 8;
}else if(cutStepMode==4) {
  actualLength=actualLength * 16;
  stripSteps=stripSteps * 16;
  aCycle = aCycle * 16;
}
//Set ms1,ms2,ms3 pins for step mode
   if(cutStepMode==4){
   digitalWrite(ms1B,HIGH);      //going to do this at 1/16 step
   digitalWrite(ms2B,HIGH);
   digitalWrite(ms3B,HIGH);
   }else if(cutStepMode==3) {
   digitalWrite(ms1B,HIGH);      //going to do this at 1/8 step
   digitalWrite(ms2B,HIGH);
   digitalWrite(ms3B,LOW); 
   }else if(cutStepMode==2) {
   digitalWrite(ms1B,LOW);      //going to do this at 1/4 step
   digitalWrite(ms2B,HIGH);
   digitalWrite(ms3B,LOW); 
   }else if(cutStepMode==1) {
   digitalWrite(ms1B,HIGH);      //going to do this at 1/2 step
   digitalWrite(ms2B,LOW);
   digitalWrite(ms3B,LOW);
   }else {
   digitalWrite(ms1B,LOW);      //going to do this at full step
   digitalWrite(ms2B,LOW);
   digitalWrite(ms3B,LOW);
   }
   
 delay(1000);
 openCutter();  //open cutter to 0 position 
 while(Serial.available()){Serial.read();} 
}


void loop() {       
 if(Serial.available()) {
    dfd += char(Serial.read());   //read data on serial
   }

 //check for cut command(s)
    if((dfd.substring(0,3)=="cut") & (dfd.length()==10)) {    
     if(dfd.substring(3,4)=="1") preStripValue = float(dfd.substring(5).toInt()) / 10;
     if(dfd.substring(3,4)=="2") lengthValue = float(dfd.substring(5).toInt()) / 10;
     if(dfd.substring(3,4)=="3") postStripValue = float(dfd.substring(5).toInt()) / 10;
     if(dfd.substring(3,4)=="4") {
      uom = dfd.substring(4,5);
      qtyValue = dfd.substring(5).toInt();
      delay(50);
      dfd="";
      cutLoop();
      while(Serial.available()){Serial.read();}   //clear serial buffer of anything sent after loop completed.
      delay(100);
     }
    dfd=""; 
    }

 
 //Check for feed command(s)
   else if(((dfd.substring(0,3)=="DIN") or (dfd.substring(0,3)=="OUT")) & (dfd.length()==6)) {    //Recieved command to Feed
    vDirection = dfd.substring(0,3);                      //set vDirectino to xxx of xxx010 to be in used in Feed loop
    vLength = dfd.substring(3).toInt();                   //set vLength to xxx of DINxxx, also convert to integer 
    delay(50);
    feedLoop();
    while(Serial.available()){Serial.read();}   //clear serial buffer of anything sent after loop completed.
    delay(100);
    dfd="";
   }
 
 //check for load assist command
 else if((dfd.substring(0,5)=="WPREP") & (dfd.length()==5)) {     //Recieved command to assist load
  loadAssist();
  while(Serial.available()){Serial.read();}   //clear serial buffer of anything sent after loop completed.
  delay(100);
  dfd = ""; 
 }
 
 //check for test command(s)
  else if((dfd.substring(0,5)=="MTEST") & (dfd.length()==6)) {    //Recieved command to Test (MTEST1 MTEST2 MTEST3)
   vMotor = dfd.substring(5).toInt();                             //set vMotor to 1,2,or 3 to determine which motor to run in testLoop
   delay(50);
   testLoop();
   while(Serial.available()){Serial.read();}   //clear serial buffer of anything sent after loop completed.
   delay(100);
   dfd = ""; 
  }

 //Check for step move (steptst) command(s)
  else if(((dfd.substring(6)=="DIN") or (dfd.substring(6)=="OUT")) & (dfd.length()==9)) {
   vMode = dfd.substring(0,1).toInt();
   vStep = dfd.substring(2,6).toInt();
   sMotor = dfd.substring(1,2);
   vDirection = dfd.substring(6);
   delay(50);
   steptst();
   while(Serial.available()){Serial.read();}   //clear serial buffer of anything sent after loop completed.
   delay(100);
   dfd = "";
  }

}


//----------------------LOOP FOR CUTTING WIRE-----------------------------------------  STOPPED HERE, NEED TO REVERSE STEPPERS AS A is FEED, B is CUT (or verify them), ALSO NEED TO SET STEP MODE etc
void cutLoop() {
  delay(500);                     //delay to let screen catch up
  Serial.print("vis go,0");       //change to status page
  Serial.write(0xff);
  Serial.write(0xff);
  Serial.write(0xff);
  delay(300);
  Serial.print("t2.txt=\"Running..\"");    //change status
  Serial.write(0xff);
  Serial.write(0xff);
  Serial.write(0xff);
  delay(300);

  while(Serial.available()){Serial.read();}   //clear serial buffer of any lagging junk from screen/variable change. Sometimes the 0xff write is caught in buffer and interrupts myStop check.

  digitalWrite(enablePinA,LOW); //enable stepperA
  digitalWrite(enablePinB,LOW); //enable stepperB  
  delay(300);

  if(uom=="I") {    //input is in inches. Convert to mm for standard processing.
    preStripValue = preStripValue * 25.4;
    lengthValue = lengthValue * 25.4;
    postStripValue = postStripValue * 25.4;
  }
  
  for(int a = 1; a < (qtyValue + 1); a++) {         //loop 1 for each qty entered
   if(Serial.available() & (vRun==1)) {      //checking serial data again, in case STOP is sent
      myStop = char(Serial.read()); 
   }
    if((myStop=="S")){        //if STOP is rcvd then exit the loop
    Serial.print("t2.txt=\"STOP !\"");
    Serial.write(0xff);
    Serial.write(0xff);
    Serial.write(0xff);
    delay(1000);
    dfd="";
    myStop="";
    vRun=0;
    break;
     }
    else { 
    Serial.print("t1.txt=\"" + String(a) + " of " + String(qtyValue) + "\"");
    Serial.write(0xff);
    Serial.write(0xff);
    Serial.write(0xff);
    
   if(preStripValue > 0){   //only run if preStripValue was entered
    //Code to run FEED motor for preCut Strip Cut
    float preCutL = preStripValue * actualLength;       //multiply input by actualLength(int variable set at start)
    int newPreCutL = round(preCutL); //round to whole number for loop below
    digitalWrite(dirPinA,LOW);         //set feed direction to CCW to feed wire
    digitalWrite(enablePinA,LOW);      //enable feed driver
    for(int x = 0; x < newPreCutL; x++) {   
     digitalWrite(stepPinA,HIGH);
     delayMicroseconds(500);         //this controls the speed of the turn. 500 is pretty smooth but 900 is slower
     digitalWrite(stepPinA,LOW);
     delayMicroseconds(500);
   }
   delay(500);
    stripCutter();   //loop that will close strip cutter using stripSteps, then opens cutter
   }
   
    //Code to run FEED motor for actual Length (dirPinA still set HIGH from 1st preCut)
    float cutL = lengthValue * actualLength;       //multiply input by actualLength(int variable set at start)
    int newCutL = round(cutL); //round to whole number for loop below
    for(int x = 0; x < newCutL; x++) {  
     digitalWrite(stepPinA,HIGH);
     delayMicroseconds(500);         //this controls the speed of the turn. 500 is pretty smooth but 900 is slower
     digitalWrite(stepPinA,LOW);
     delayMicroseconds(500);
   }
   delay(500);

  if(postStripValue > 0){   //only run if postStripValue was entered   
   stripCutter();   //loop that will close strip cutter using stripSteps, then opens cutter
   float postCutL = postStripValue * actualLength;       //multiply input by actualLength(int variable set at start)
   int newPostCutL = round(postCutL);  //round to whole number for loop below
   digitalWrite(dirPinA,LOW);         //set feed direction to CCW to feed wire
   digitalWrite(enablePinA,LOW);      //enable feed driver 
   for(int x = 0; x < newPostCutL; x++) {   //multiply input by 6.23 because it takes 623 steps for 100mm, so 6.23 for 1mm (+/- mm)
     digitalWrite(stepPinA,HIGH);
     delayMicroseconds(500);         //this controls the speed of the turn. 500 is pretty smooth but 900 is slower
     digitalWrite(stepPinA,LOW);
     delayMicroseconds(500);
   }
   delay(500);
  }
  
    //Code to run CUT motor for final Cut (dirPinB still set LOW from precut)
   closeCutter();
   openCutter();
   delay(1000);   //end of cut delay
   }
    myStop="";
  }
  
    digitalWrite(enablePinA,HIGH); //disable driveA
    digitalWrite(enablePinB,HIGH); //disable driveB
    digitalWrite(dirPinA,LOW);    //not needed, but why keep dir pin HIGH if not in-use
    digitalWrite(dirPinB,LOW);    //not needed, but why keep dir pin HIGH if not in-use
    delay(300);
    Serial.print("cut.n3.val=0");       //reset quantity on cut page
    Serial.write(0xff);
    Serial.write(0xff);
    Serial.write(0xff);
    delay(1000);
    Serial.print("t1.txt=\"DONE!\"");
    Serial.write(0xff);
    Serial.write(0xff);
    Serial.write(0xff);
    delay(1000);
    Serial.print("page start");
    Serial.write(0xff);
    Serial.write(0xff);
    Serial.write(0xff);      
    delay(500);
    Serial.print("page start");
    Serial.write(0xff);
    Serial.write(0xff);
    Serial.write(0xff); 
    dfd="";
    vRun=1;
 }
//------------------------------------------------------------------------------------

//----------------------LOOP FOR FEEDING WIRE-----------------------------------------
void feedLoop() {
  //This loop is to run the feed stepper using
  //vDirection = DIN or DOUT for clockwise or counterclockwise direction
  //vLength = 001/010/100 for mm to travel
  digitalWrite(enablePinA,LOW); //enable driveA
  //run feed motor
  if(vDirection=="DIN"){
   digitalWrite(dirPinA,LOW);  //spin CCW
  }
  else{
    digitalWrite(dirPinA,HIGH);  //spin CW
  }
  if(vLength==001){
    for(int x = 0; x < (1 * aCycle); x++) {   
     digitalWrite(stepPinA,HIGH);
     delayMicroseconds(500);         //this controls the speed of the turn. 500 is pretty smooth but 900 is slower
     digitalWrite(stepPinA,LOW);
     delayMicroseconds(500);
   }
  }

  if(vLength==10){
    for(int x = 0; x < (10 * aCycle); x++) {   
     digitalWrite(stepPinA,HIGH);
     delayMicroseconds(500);         //this controls the speed of the turn. 500 is pretty smooth but 900 is slower
     digitalWrite(stepPinA,LOW);
     delayMicroseconds(500);
   }
 }
  
 if(vLength==100){
    for(int x = 0; x < (100 * aCycle); x++) {   
     digitalWrite(stepPinA,HIGH);
     delayMicroseconds(500);         //this controls the speed of the turn. 500 is pretty smooth but 900 is slower
     digitalWrite(stepPinA,LOW);
     delayMicroseconds(500);
   }
 }
 
   digitalWrite(dirPinA,LOW);  
   delay(1000);
 //Serial.print("feed loop " + (vDirection) + " : " + String(vLength));
 
 digitalWrite(enablePinA,HIGH); //disable driveA
 dfd="";
}
//------------------------------------------------------------------------------------

//----------------------LOOP FOR LOAD ASSIST------------------------------------------
void loadAssist() {
//Feed in around 80mm of wire, then cut.
  openCutter();
  delay(500);
  digitalWrite(enablePinA,LOW); //enable driveA
  //run feed motor
   digitalWrite(dirPinA,LOW);  //spin CCW
    for(int x = 0; x < (80 * aCycle); x++) {    //feed ~80mm of wire
     digitalWrite(stepPinA,HIGH);
     delayMicroseconds(500);         
     digitalWrite(stepPinA,LOW);
     delayMicroseconds(500);
   }
  digitalWrite(dirPinA,LOW);  
   delay(1000);
 digitalWrite(enablePinA,HIGH); //disable driveA
 //cut any excess wire that feed out
 closeCutter();
 delay(500);
 openCutter();
 delay(500);
 dfd="";
}
//------------------------------------------------------------------------------------

//----------------------LOOP FOR TESTING MOTORS---------------------------------------
void testLoop() {
 delay(300);     //delay to let screen catch up 
if(vMotor==1){    //test Feed motor
   digitalWrite(enablePinA,LOW); //enable driveA
   //Code to run FEED motor Counter Clockwise
   digitalWrite(dirPinA,LOW);  
    for(int x = 0; x < (100 * aCycle); x++) {   
     digitalWrite(stepPinA,HIGH);
     delayMicroseconds(500);         
     digitalWrite(stepPinA,LOW);
     delayMicroseconds(500);
   }
   digitalWrite(dirPinA,HIGH);
   delay(1000);
   //Code to run FEED motor Clockwise
    for(int x = 0; x < (100 * aCycle); x++) {   
     digitalWrite(stepPinA,HIGH);
     delayMicroseconds(500);         
     digitalWrite(stepPinA,LOW);
     delayMicroseconds(500);
   }   
   delay(1000);
   digitalWrite(enablePinA,HIGH); //disable driveA
   digitalWrite(dirPinA,LOW);
 }else if(vMotor==2){      //test CUT motor
  closeCutter();
  openCutter();
 }
  dfd="";
}
//------------------------------------------------------------------------------------

//----------------------LOOP FOR STEP TEST OF MOTORS----------------------------------
void steptst() {
  //Serial.println("Mode:" + String(vMode) + " , Step:" + String(vStep) + " , Motor:" + String(sMotor) + " , Dir:" + String(vDirection));
  //Set step mode to whatever user has choosen
   if(vMode==4) {                //mode is 1/16 step
    digitalWrite(ms1A,HIGH);
    digitalWrite(ms2A,HIGH);
    digitalWrite(ms3A,HIGH);
   }
   else if(vMode==3) {           //mode is 1/8 step
    digitalWrite(ms1A,HIGH);
    digitalWrite(ms2A,HIGH);
    digitalWrite(ms3A,LOW);
   }
   else if(vMode==2) {           //mode is 1/4 step
    digitalWrite(ms1A,LOW);
    digitalWrite(ms2A,HIGH);
    digitalWrite(ms3A,LOW);
   }
   else if(vMode==1) {           //mode is 1/2 step
    digitalWrite(ms1A,HIGH);
    digitalWrite(ms2A,LOW);
    digitalWrite(ms3A,LOW);
   }
   else if(vMode==0) {           //mode is full step
    digitalWrite(ms1A,LOW);
    digitalWrite(ms2A,LOW);
    digitalWrite(ms3A,LOW);
   }

//If spinning feed stepper    
  if(sMotor=="F") {               //Setup Feed Motor
   if(vDirection=="DIN") {        //Set direction
    digitalWrite(dirPinA,HIGH);
   }
   else{
    digitalWrite(dirPinA,LOW);
   }
   //Code to run motor 
   digitalWrite(enablePinA,LOW); //enable driveA
   for(int x = 0; x < vStep; x++) {   
     digitalWrite(stepPinA,HIGH);
     delayMicroseconds(500);         
     digitalWrite(stepPinA,LOW);
     delayMicroseconds(500);
   }
   digitalWrite(enablePinA,HIGH); //disable driveA
   delay(1000);
   
 }
//If spinning cut stepper  
 else if(sMotor=="C") {          //Setup Cut Motor
   //Code to run motor 
   digitalWrite(enablePinB,LOW); //enable driveB
   if(vDirection=="DIN") {    //motor is being stepped in CW direction (cut)
    digitalWrite(dirPinB,HIGH);
    for(int x = 0; x < vStep; x++) {
        digitalWrite(stepPinB,HIGH);
        delayMicroseconds(500);         
        digitalWrite(stepPinB,LOW);
        delayMicroseconds(500);
    } //close step loop
   }else {    //motor is being stepped in CCW direction (open)
    digitalWrite(dirPinB,LOW);
    for(int x = 0; x < vStep; x++) {
        digitalWrite(stepPinB,HIGH);
        delayMicroseconds(500);         
        digitalWrite(stepPinB,LOW);
        delayMicroseconds(500);
    } //close step loop
   }
   digitalWrite(enablePinB,HIGH); //disable driveB
   delay(500);
 }

 //Set ms1,ms2,ms3 pins for step mode back to default for running.
   if(cutStepMode==4){
   digitalWrite(ms1B,HIGH);      //going to do this at 1/16 step
   digitalWrite(ms2B,HIGH);
   digitalWrite(ms3B,HIGH);
   }else if(cutStepMode==3) {
   digitalWrite(ms1B,HIGH);      //going to do this at 1/8 step
   digitalWrite(ms2B,HIGH);
   digitalWrite(ms3B,LOW); 
   }else if(cutStepMode==2) {
   digitalWrite(ms1B,LOW);      //going to do this at 1/4 step
   digitalWrite(ms2B,HIGH);
   digitalWrite(ms3B,LOW); 
   }else if(cutStepMode==1) {
   digitalWrite(ms1B,HIGH);      //going to do this at 1/2 step
   digitalWrite(ms2B,LOW);
   digitalWrite(ms3B,LOW);
   }else {
   digitalWrite(ms1B,LOW);      //going to do this at full step
   digitalWrite(ms2B,LOW);
   digitalWrite(ms3B,LOW);
   }
}
//------------------------------------------------------------------------------------

void openCutter() {
   digitalWrite(enablePinB,LOW); //enable driveB
   digitalWrite(dirPinB,LOW);     //will be turning CCW to open
   for(int x = 0; x < openSteps; x++) {      
     digitalWrite(stepPinB,HIGH);
     delayMicroseconds(500);         
     digitalWrite(stepPinB,LOW);
     delayMicroseconds(500);
    }
   digitalWrite(enablePinB,HIGH); //disable driveB
   delay(800);
}

void closeCutter() {
   digitalWrite(enablePinB,LOW); //enable driveB
   digitalWrite(dirPinB,HIGH);    //will be turning CW to close
   for(int x = 0; x < closeSteps; x++) {      
     digitalWrite(stepPinB,HIGH);
     delayMicroseconds(500);         
     digitalWrite(stepPinB,LOW);
     delayMicroseconds(500);
   }
   digitalWrite(enablePinB,HIGH); //disable driveB
   delay(800);
}

void stripCutter() {
   digitalWrite(enablePinB,LOW);  //enable driveB
   digitalWrite(dirPinB,HIGH);    //will be turning CW to close for strip step
   for(int x = 0; x < stripSteps; x++) {      
     digitalWrite(stepPinB,HIGH);
     delayMicroseconds(500);         
     digitalWrite(stepPinB,LOW);
     delayMicroseconds(500);
   }
   delay(300);
   digitalWrite(dirPinB,LOW);    //will be turning CCW to open back after strip close
   for(int x = 0; x < stripSteps; x++) {      
     digitalWrite(stepPinB,HIGH);
     delayMicroseconds(500);         
     digitalWrite(stepPinB,LOW);
     delayMicroseconds(500);
   }
   digitalWrite(enablePinB,HIGH); //disable driveB
   delay(300);
}


  

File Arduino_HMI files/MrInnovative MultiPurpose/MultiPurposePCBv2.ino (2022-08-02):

 //#include <Nextion.h>    //used for MCU through HMI Editor only -- must remove or comment out when using actual screen
//#define nextion Serial  //used for MCU through HMI Editor only -- must remove or comment out when using actual screen

//-------------User Variables------------------------------------------------------------------------------------------------------------------------------------------------------------
//  These may change depending upon the setup: Stepper steps for rotation, Stepper mode, etc
//  My steppers are 200 full steps for a full rotation (360 degrees), so numbers below based on that.
//  Should be the only variables that would need to be changed in code.
float actualLength = 6.23;      //will be used in cutLoop for steps per mm      **I've calculated 623 steps for 100mm, so 623/100=6.23 which should be 1mm. Change this value as required.
int aCycle = round(actualLength); //dont change this line, used in loops for Cut loop, Feed loop, Load assist loop, Testing Motors loop - loops should be whole numbers only.
//<-----Making the below values big for testing. 200 steps should be a full 360° spin----->
int stripSteps = 200;          //total steps needed for Cutter to make STRIP cut --will need to adjust depending upon wire AWG and your setup.
int cutOpenSteps = 400;        //Steps to open cutters from a close (cut) position
int cutCloseSteps = 400;       //Steps to close cutters from a open position

//---------------------------------------------------------------------------------------------------------------------------------------------------------------------------------------

//Pin assigments
const int stepEnable = 12;   //Stepper(s) Enable Pin
const int stepADir = A0;     //Stepper1 Direction Pin
const int stepAStep = A1;    //Stepper1 Step Pin
const int stepBDir = A2;     //Stepper2 Direction Pin
const int stepBStep = A3;    //Stepper2 Step Pin

//---Variables----------------------------------------------------------------------------------
String dfd = "";                //Serial data container, data from display

//CutLoop variables, sent from cut page
float preStripValue = 0;      //will be used to store precut(strip) for cutLoop
float lengthValue = 0;        //will be used to store cut length for cutLoop
float postStripValue = 0;     //will be used to store postcut (strip) for cutLoop
int qtyValue = 0;             //will be used to store qty for cutLoop
String uom = "";              //will be used as unit of measure (I=inch, M=mm)
String myStop = "";           //will be used in cutLoop to monitor for STOP being pressed
int vRun = 1;                 //will be used in cutLoop to interrupt if STOP pressed

//feedLoop variables, sent from feed page  - feed wire in/out    (vDirection, vLength)
String vDirection = "";
unsigned long vLength;    

//testLoop variables, sent from test page  - cycle steppers      (vMotor)
int vMotor;     //might be able to change to String 
 
//stepLoop variables, sent from steptst page - run stepper x pulses , x step mode
//will use vDirection (variable above in feedLoop) for step direction 
int vStep = 0;                //Steps to take
String sMotor = "";
int vMode = 0;    //wont be used

//-----------------------------------------------------------------------------------------------

void setup() {
 Serial.begin(9600);                  
 pinMode(stepEnable, OUTPUT);

 pinMode(stepAStep, OUTPUT);
 pinMode(stepADir, OUTPUT);
 pinMode(stepBStep, OUTPUT);
 pinMode(stepBDir, OUTPUT);
 delay(500);

 openCutter();                       //Open cutter. No way to know what position they are in so will open to atleast be consistent.
 while(Serial.available()){Serial.read();} 
 
}


void loop() {       
 if(Serial.available()) {
    dfd += char(Serial.read());   //read data on serial if recieved, store all in dfd variable
   }

 //check for 'cut' command. This will be sent from nextion status page 'START' button being pressed.
 //Nextion data sent will be 4 lines:
 //cut1M00010           <--- will contain the 1st strip length
 //cut2M00550           <--- will contain the wire length
 //cut3M00010           <--- will contain 2nd strip length
 //cut4M00008           <--- will contain qty
    if((dfd.substring(0,3)=="cut") & (dfd.length()==10)) {                                //if first 3 characters recieved are 'cut' and the total characters are 10 then do this:
     if(dfd.substring(3,4)=="1") preStripValue = float(dfd.substring(5).toInt()) / 10;    //if the 4th char is '1' then this is the 1st strip length line (cut1) set preStripValue to number(s) after 5th char and divide by 10.
     if(dfd.substring(3,4)=="2") lengthValue = float(dfd.substring(5).toInt()) / 10;      //if the 4th char is '2' then this is the wire length line (cut2) set lengthValue to number(s) after 5th char and divide by 10.
     if(dfd.substring(3,4)=="3") postStripValue = float(dfd.substring(5).toInt()) / 10;   //if the 4th char is '3' then this is the 2nd strip length line (cut3) set postStripValue to number(s) after 5th char and divide by 10.
     if(dfd.substring(3,4)=="4") {                                                        //if the 4th char is '4' then this is the qty line (cut4) set uom to the 4th character, and qtyValue to number(s) after 5th char.
      uom = dfd.substring(4,5);
      qtyValue = dfd.substring(5).toInt();
      delay(50);
      dfd="";
      cutLoop();                                                                          //with all variables needed collected, run cutLoop function.
      while(Serial.available()){Serial.read();}                                           //clear serial buffer of anything sent after loop completed.
      delay(100);
     }
    dfd=""; 
    }
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

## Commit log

2021-09-06 Add files via upload
    Fixed feed assit back button to page
2021-09-07 Update current issues to work out.txt
2021-09-09 Add files via upload
    Modified to change limit switch assignment on startup, if not what is expected. Found that I kept plugging switches into wrong connectors and this could potentially break a part as the motor would spin past the limit switch.
2021-10-25 Update What to print.txt
2021-11-18 Delete arduino_ino/cutter_no_limit_sw directory
    Not updated for no limit switch, so removing and working on
2022-08-01 arduino with_limit_switch cut length updated
    Added float variables to adjust if decimal used in length values.
2022-08-01 Updated folder structure
    Tried to make file structure easier to follow. With different sources for different build(s), under Arduino_HMI files folder.
    Also updated arduino code under 'My WireCutter with Limit Switchs' to use float values where needed for length to take into account decimal value entered.
    [40mm_Hexaguard.stl, BOM_Ext_5v.csv, BOM_PCB_WireCutter_v2.0_2021-08-30.csv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]
